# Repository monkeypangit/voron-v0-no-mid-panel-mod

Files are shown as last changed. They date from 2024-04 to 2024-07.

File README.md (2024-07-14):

# Voron Zero - No mid panel mod

&nbsp;<br>
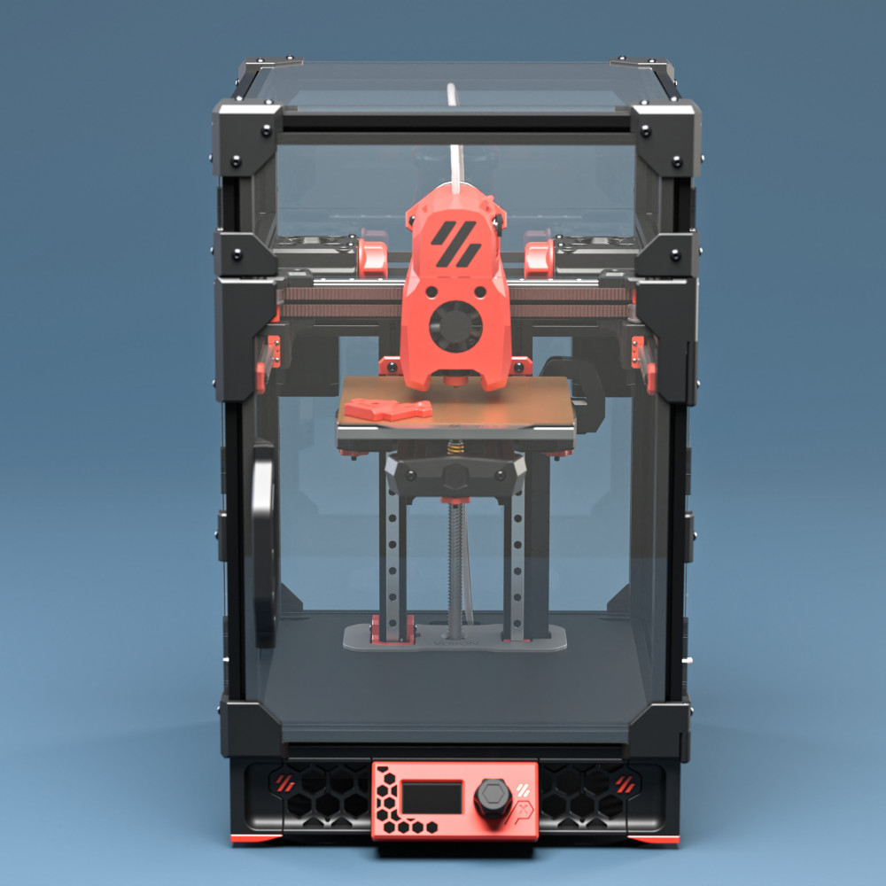
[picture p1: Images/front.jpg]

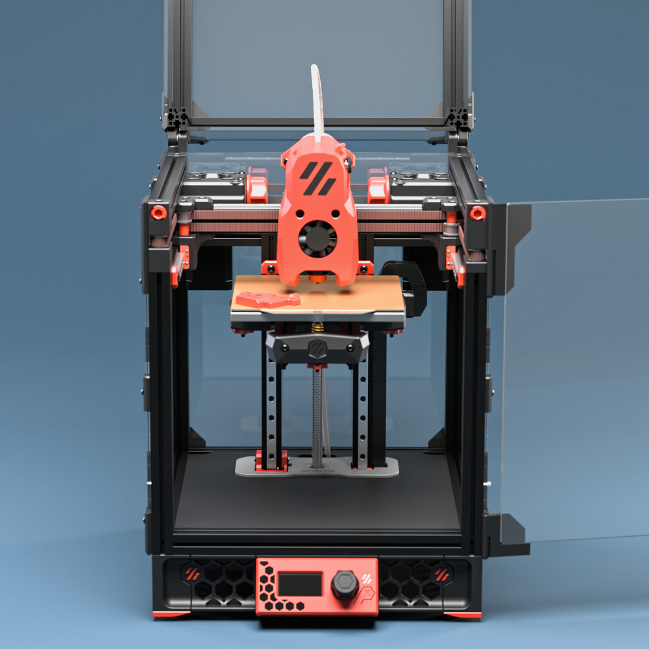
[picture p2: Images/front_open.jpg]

&nbsp;<br>
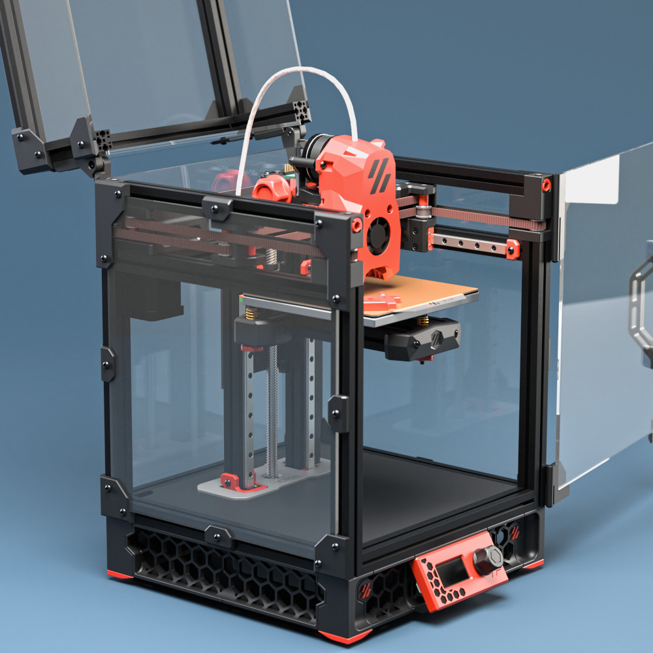
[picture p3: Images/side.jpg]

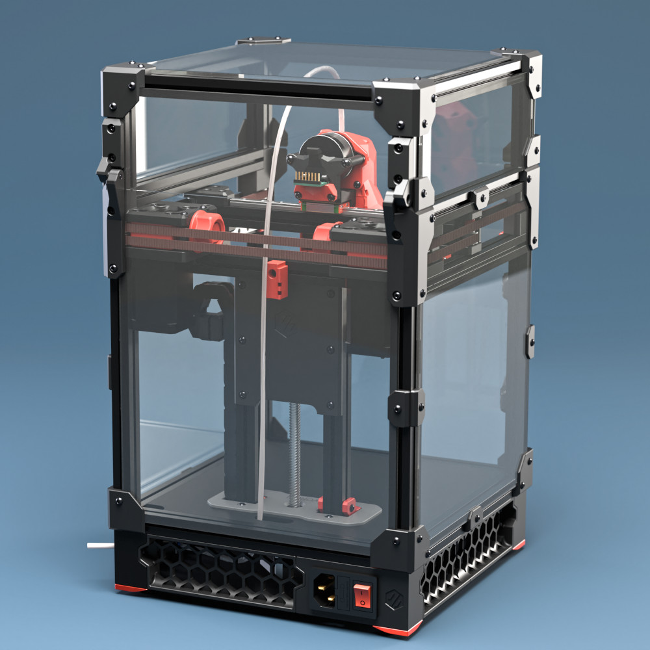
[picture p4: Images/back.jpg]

&nbsp;<br>

## Description
Mod for the Voron Zero that does away with the mid panel and replaces it with a printed brace.

## Status
This mod is in alpha/beta. It has only been built by me so far. There are some known issues listed below that may or may not be fixed at some point...

## Print settings
Print according to official Voron [print settings](https://docs.vorondesign.com/sourcing.html#print-settings).

## Bom
* Transparent back panel.
* Meanwell IRM-90-24ST power supply
* Crydom ED24C3 solid state relay
* Bigtreetech Manta E3EZ (SKR Pico + RPi stacked vertically also works)
* AC Powered bed heater
* 2x M3x35 BHCS
* 9x M3x8 BHCS
* 2x M3x6 BHCS
* 9x M3 Nut
* 8x M3 Brass heatstake inserts - short M3x5x4

## Z frame bracket
The trick to this mod is a printed bracket that connects the z extrusions to the back extrusion. It uses two M3x35 screws for rigidity instead of the lower blind joint screw pair in the stock version.
 
&nbsp;<br>
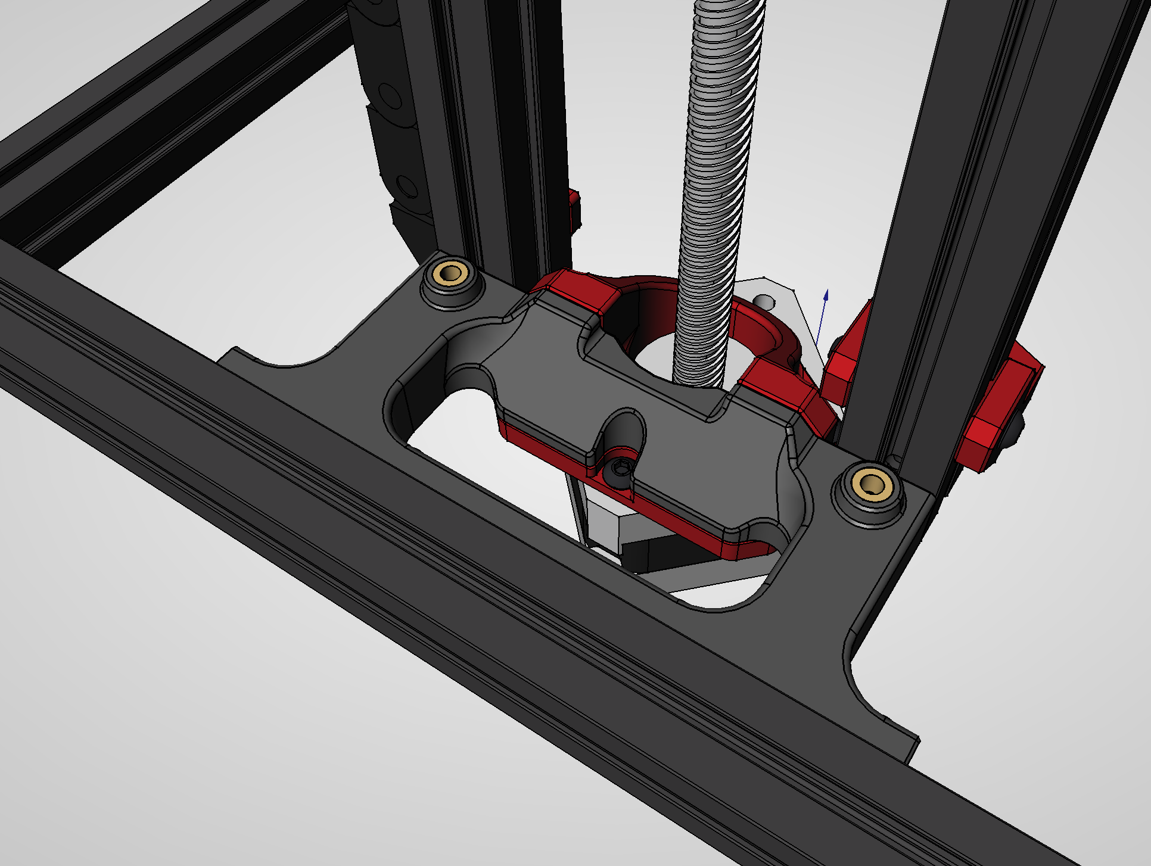
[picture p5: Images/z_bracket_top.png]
z bracket top

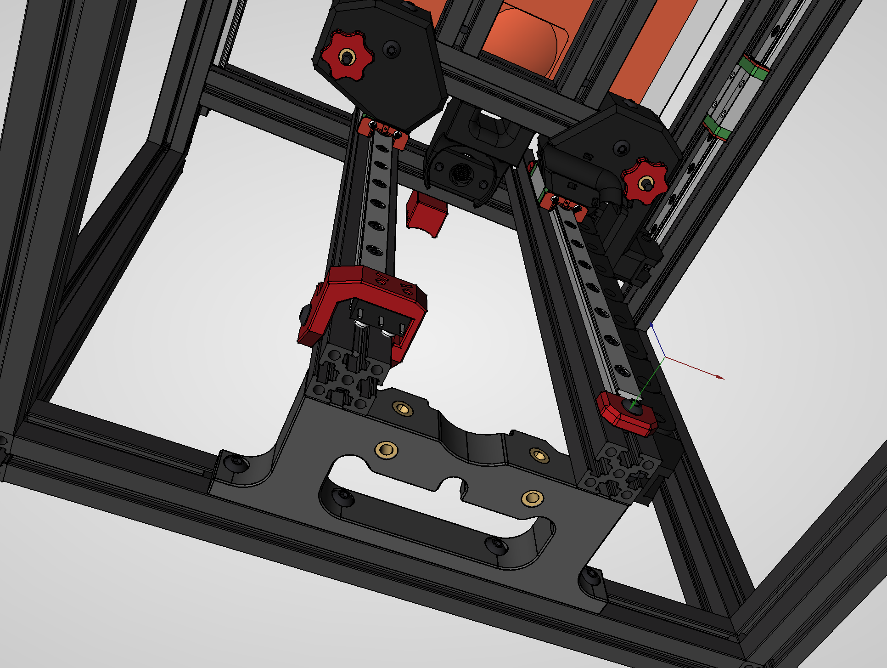
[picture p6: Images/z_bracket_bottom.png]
z bracket bottom

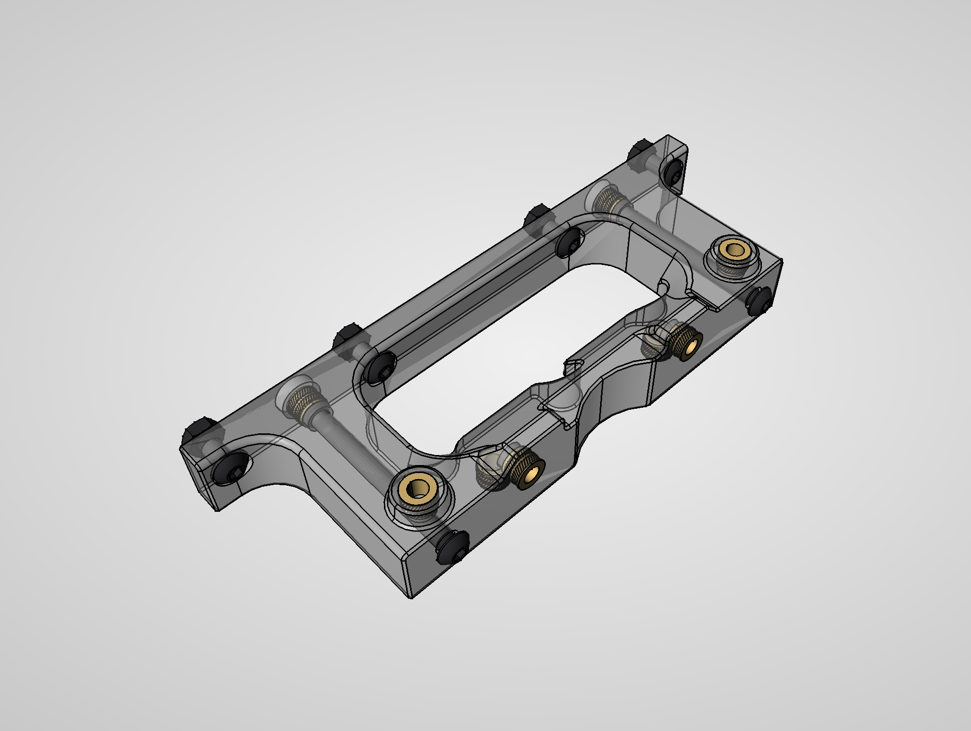
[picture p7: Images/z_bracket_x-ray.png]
z bracket x-ray

&nbsp;<br/>

## Build information
It is a fairly involved mod that requires replacing the power supply and heater from the stock BOM. It's probably best suited if you are building a self sourced v0 from scratch.

You need a working printer with a build surface that is large enough to print the 200x200mm deck panel.

The mod is designed to be as compatible as possible with other v0 mods. It retains as much as possible of the original parts.

All the electronics are moved to the bottom bay. This requires using a compact control board setup, a Meanwell IRM-90 power supply and an AC bed heater with a compact Crydom SSR.

This mod is somewhat finicky to assemble. You need to thread the deck panel and the cover plate over the z extrusions before you put the z brace in place. Here are some images go give you an idea of how the parts come together.

&nbsp;<br>
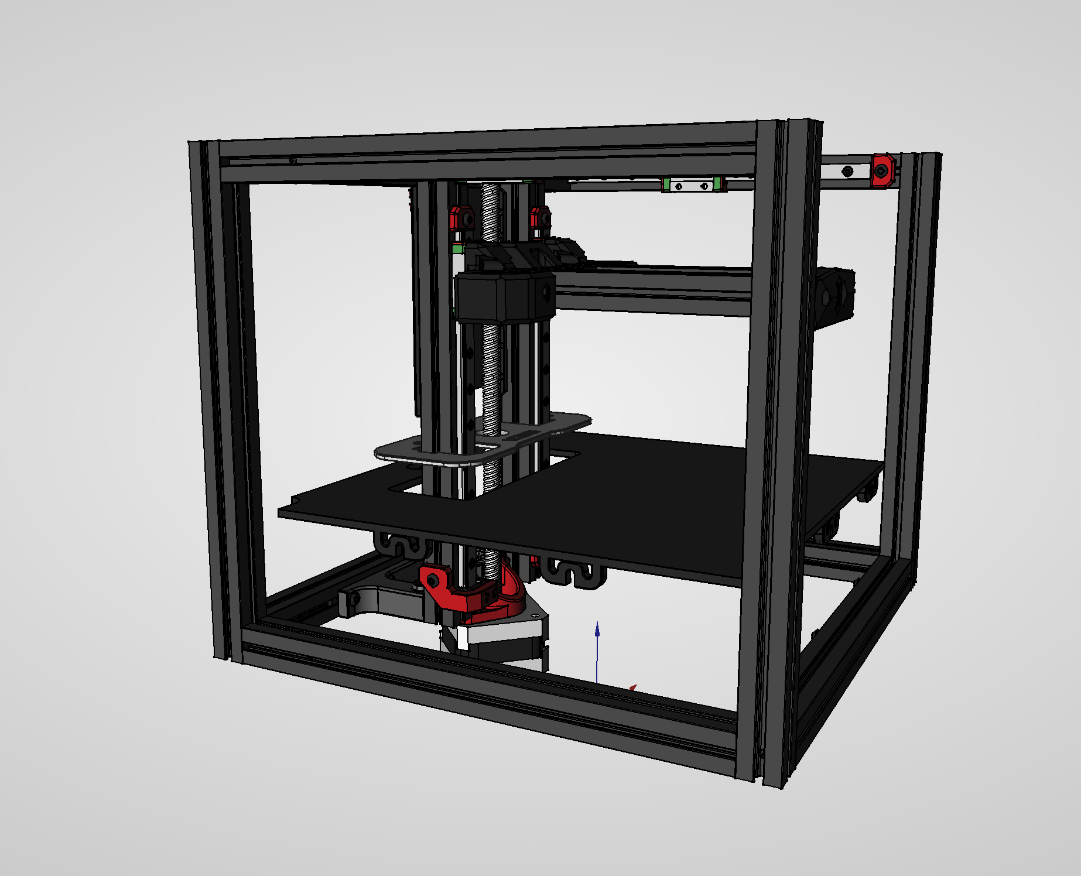
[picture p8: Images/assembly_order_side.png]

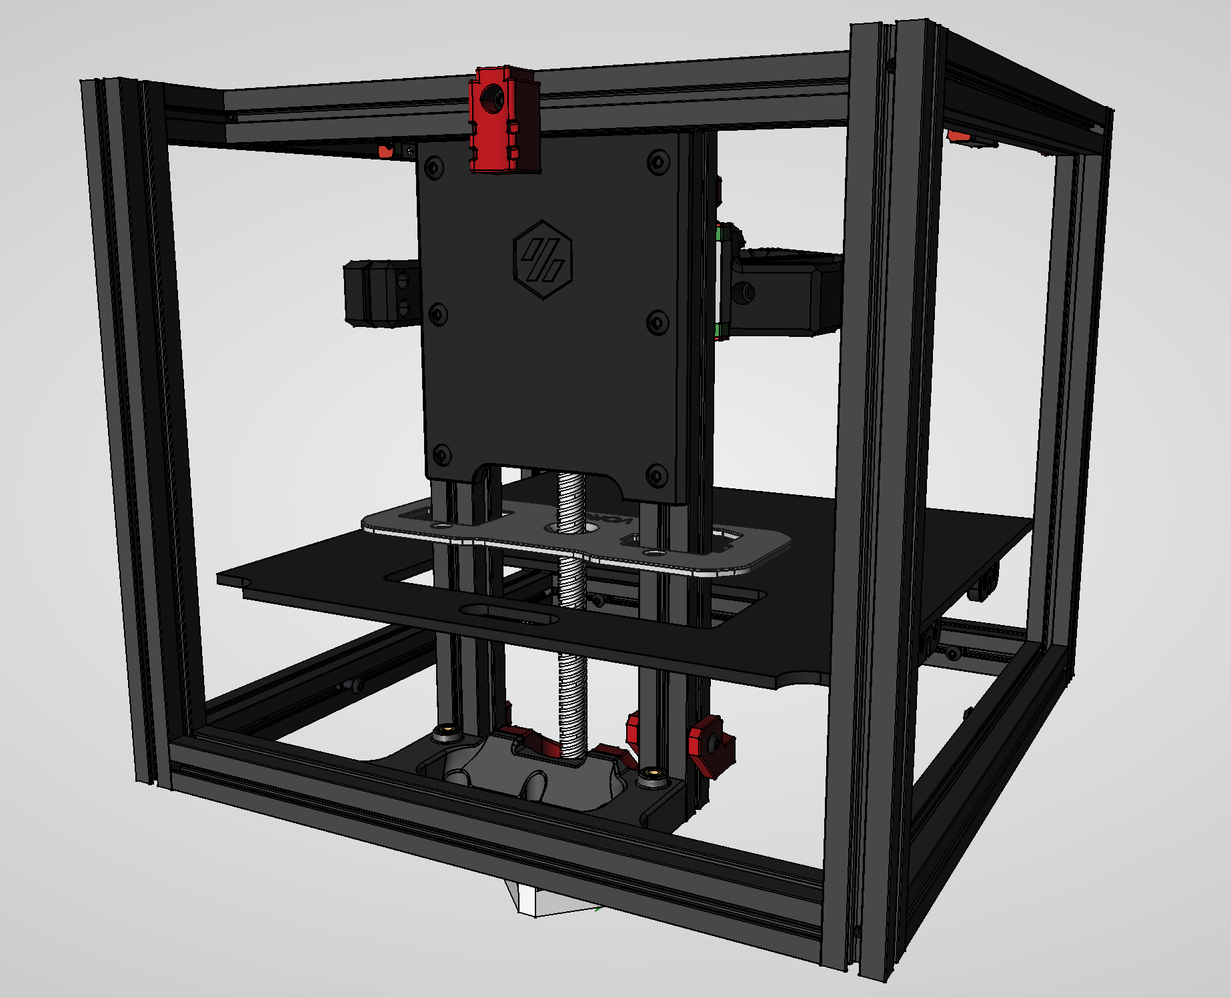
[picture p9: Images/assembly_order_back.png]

&nbsp;<br>

The printed deck panel has tabs for mounting to the bottom frame. The tabs allow for some flex to make sure the panel is rigidly mounted even if it is not exactly to size. It also has holes that allows the wires from the AB motors and toolhead to be passed through from the chamber to the electronics bay (see image below).

In the original V0 design the deck panel sits in the slot in the bottom frame. In this design the deck panel sits flush with the top of the extrusions in the bottom frame instead. You may loose a few millimiters of z-travel unless you are using a kirigami bed with a 6mm build plate and shorter bed screws.

I use this mod for a v0 build with a 170x120mm build plate (see image below). The 50mm wider frame size makes it easier to fit the compnents into the electronics bay. As far as I can tell the setup with an E3EZ should fit the stock size as well, but this is untested for now, so please do you own measurments before attempting this mod. The parts marked 170 in the stl folder is for a 170mm x build.

I recommend using a 2nd accent color for the deck panel cover if black is used as primary color.

This mod replaces the lower and upper back panel with a single transparent panel. There is no need to split these any more as there is no electronics bay in the back that requires access.

It is recommended to combine this mod with some type of fan skirt mod or to add a fan in the electronics bay (see issues).

## Chamber wiring
This image shows the intended routing of cables from the AB motors and toolhead to the electronics bay. There are cutouts in the deck panel to allow wires/cables to be passed through.

&nbsp;<br>
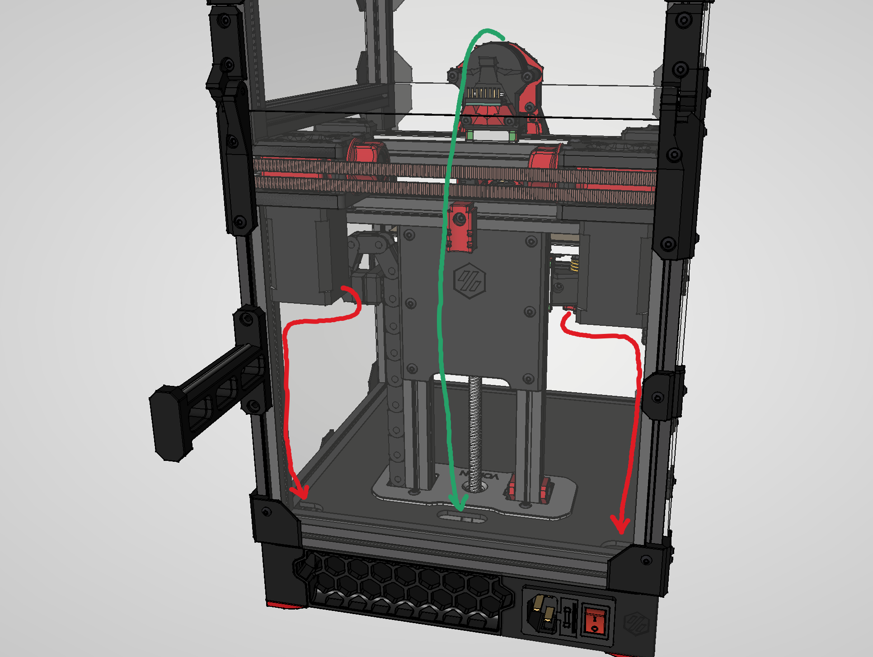
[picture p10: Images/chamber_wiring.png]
chamber wiring

&nbsp;<br/>

## Electronics bay
There are several controller boards/Pi configurations that will fit this mod. Just make sure to do some planning and measure twice oin the CAD model before you order parts.

You will have to find mounting brackets for your choice of components by yourself. I used a E3EZ with a CM4 in my build. There are STLs for the brackets for the IRM-90 and the E3EZ in the STLs folder. I stuck everything down to the deck panel with VHB tape.

Here is a youtube video by Steve Peterson where he builds a stock voron v0 with similar components for reference:

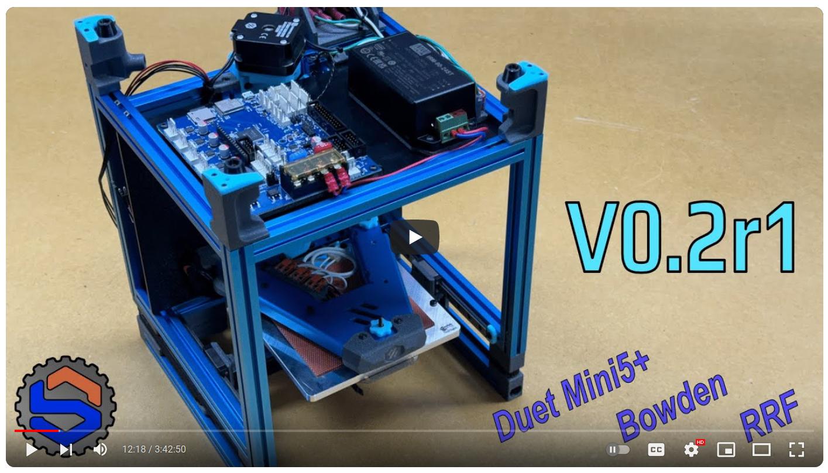
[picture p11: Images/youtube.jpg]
Steve Peterson builds a v0 with similar components


Note that he uses Reprap firmware with this build and thus he does not need a Raspberry Pi.

&nbsp;<br>
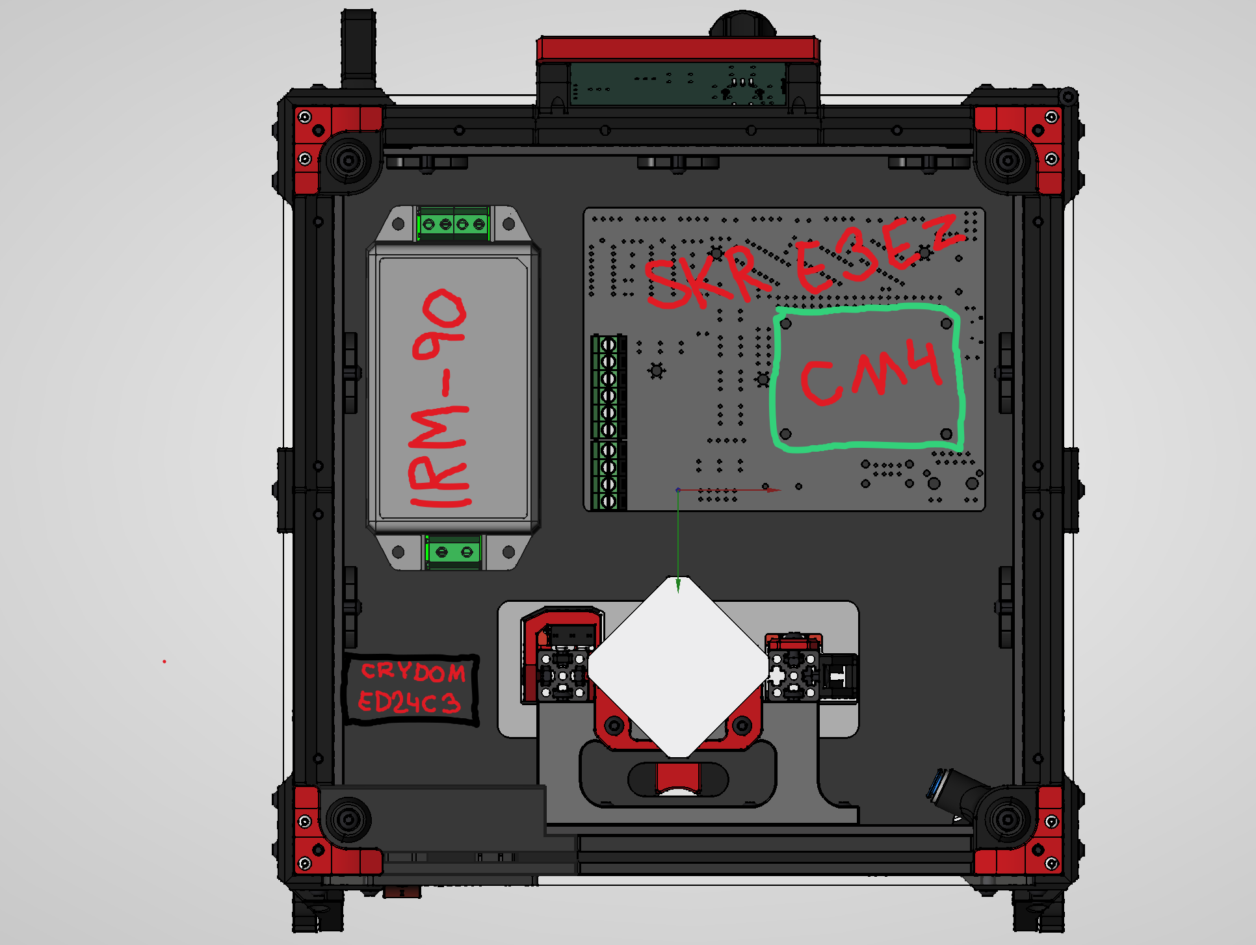
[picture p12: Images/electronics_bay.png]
electronics bay

&nbsp;<br/>

## Picture of build
Here is a picture of my build. It has a 170x120mm build area. That helps in fitting everything into the electronics bay, but from what I can measure it should work with a standard v0 as well.

I combined this with my quad cam lock mod that uses custom zero panels.

&nbsp;<br>
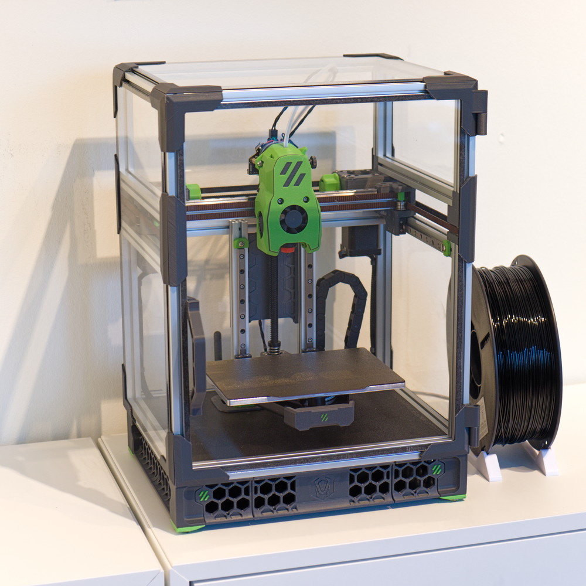
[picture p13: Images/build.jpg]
a picture of a Voron v0 with the mod installed

&nbsp;<br/>

## Known issues
* The inner pair of screws that hold the z frame bracket to the rear extrusion are tricky to reach. There are access holes for the allen key but it can be finicky...
* A split deck panel and cover would be good to simplify assembly/disassembly
* The electronics bay gets hot during pringing. I run AB motors at 0.5A RMS and Z motor at 0.3A RMS to keep things cool and sensorless homing from acting up. Probably need to add a fan somewhere in the electronics bay. There are fan skirt mods for the V0 that should fit this mod as well.
* Having the AB motors inside the enclosure makes sensorless homing more finicky to set up as the threshold values tend to vary with motor temperature.

## Disclamer
If you build this you do so at your own risk. I am not responsible if the design is incorrect or if something goes wrong. Please do your own research and act responsibly.

## Contact
Feel free to contact me here on github or as monkeyPan on the Voron Discord channel if you have questions or if you find any issues.

## Credit
Credit goes to the Voron Team for the original Voron Zero design.<br/>
[Voron team](https://github.com/VoronDesign/)<br/>

This project was inspired by the Itsy Bitsy printer by tigran on the Doomcube Discord channel.<br/>
[Itsy Bitsy by tigran](https://github.com/TigranDesigner/Voron-Mods/tree/main/Itsy%20Bitsy)

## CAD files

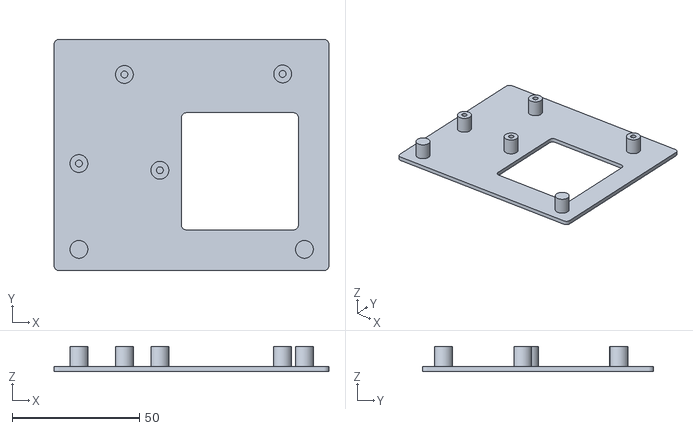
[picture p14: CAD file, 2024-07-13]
STLs/Electronics/Manta_E3EZ_Mount_x1.stl
108.0 x 90.8 x 10.0

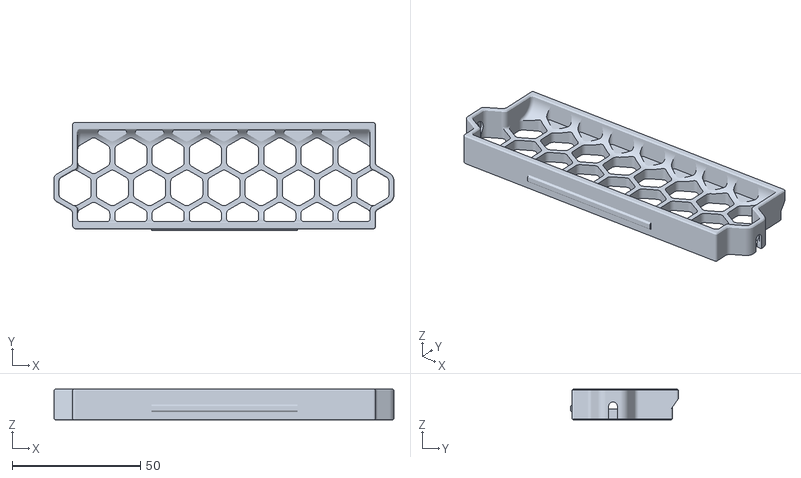
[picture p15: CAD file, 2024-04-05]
STLs/Skirts/Rear_Skirt_120_x1.stl
132.8 x 42.1 x 12.0

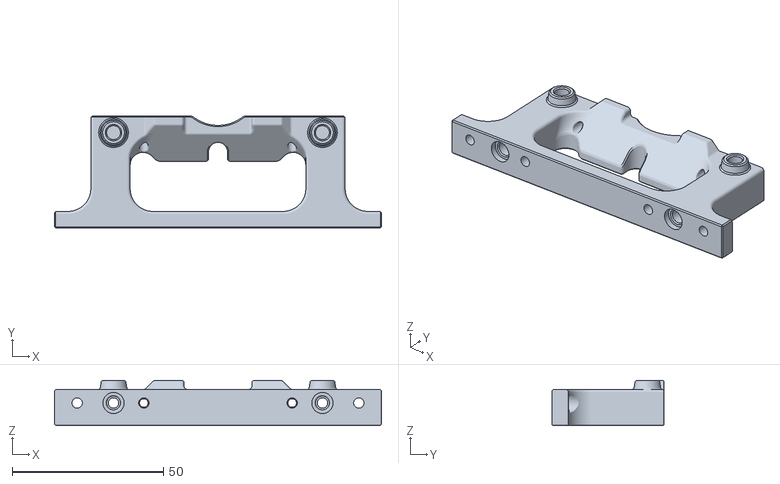
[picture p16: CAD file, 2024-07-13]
STLs/Z_Frame_Bracket_x1.stl
108.0 x 37.0 x 15.0

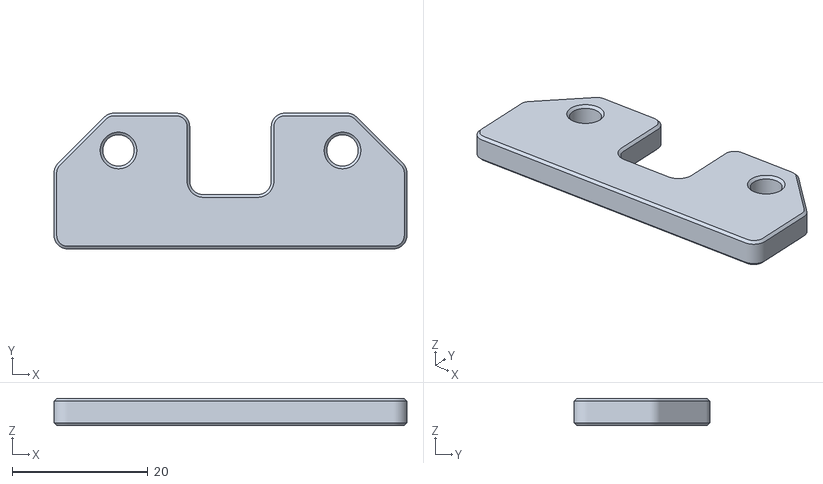
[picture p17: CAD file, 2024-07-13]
STLs/Electronics/IRM_90_24ST_Mount_x2.stl
52.0 x 20.0 x 4.00

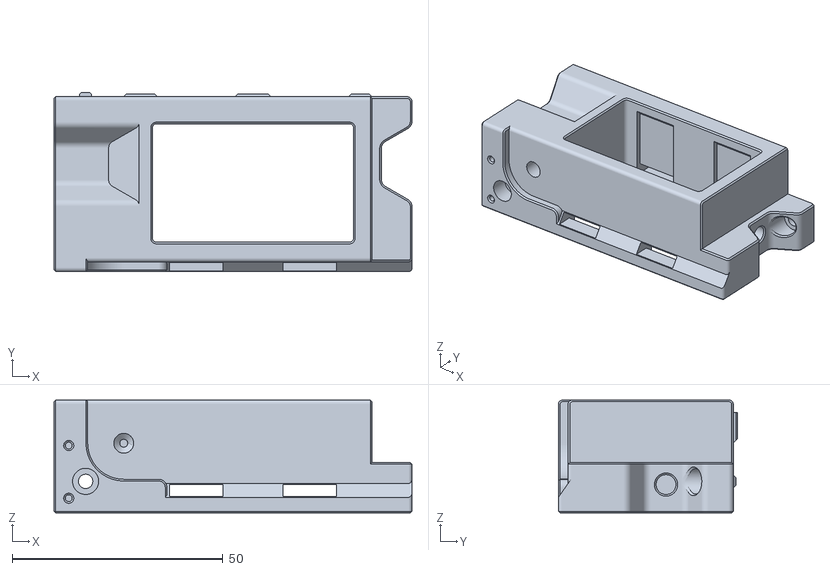
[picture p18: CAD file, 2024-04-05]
STLs/Skirts/Foot_Rear_Left_Inlet_x1.stl
84.9 x 42.5 x 26.8

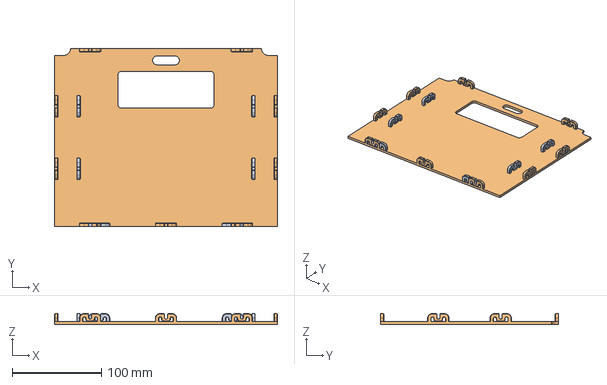
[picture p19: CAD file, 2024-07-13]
CAD/Deck Panel.FCStd
250.0 x 200.0 x 12.0 mm
Deck panel 120
Deck panel 170

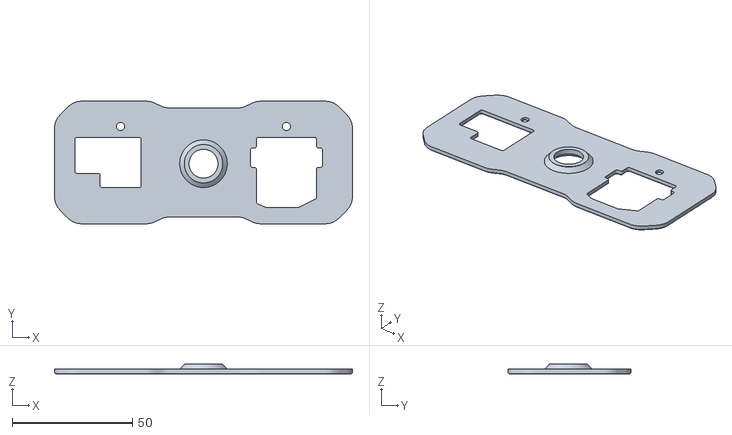
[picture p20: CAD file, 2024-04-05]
STLs/[a]_Deck Panel Cover_x1.stl
124.0 x 51.0 x 4.00

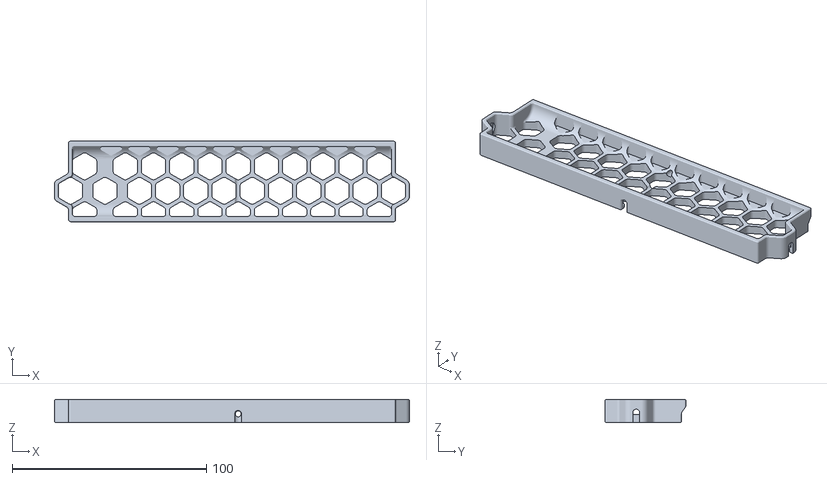
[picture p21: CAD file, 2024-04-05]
STLs/Skirts/Rear_Skirt_170_x1.stl
182.8 x 41.5 x 12.0

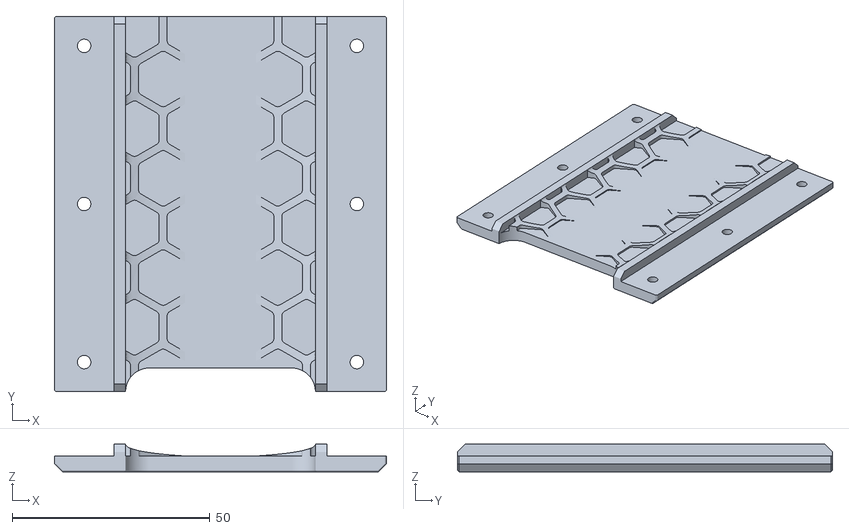
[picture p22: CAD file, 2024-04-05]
STLs/Mid_Panel_Brace_x1.stl
84.0 x 95.0 x 7.00

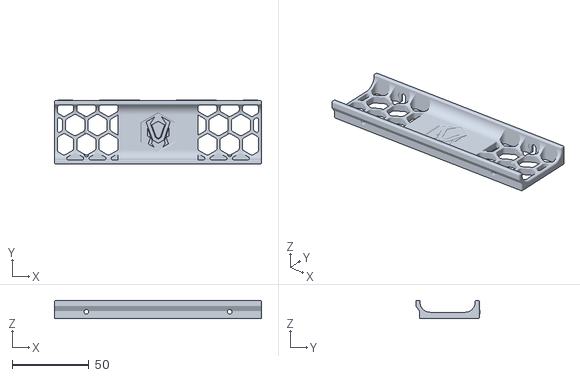
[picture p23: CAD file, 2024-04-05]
STLs/Skirts/Headless_Skirt_Insert_170_x1.stl
135.2 x 42.0 x 12.0

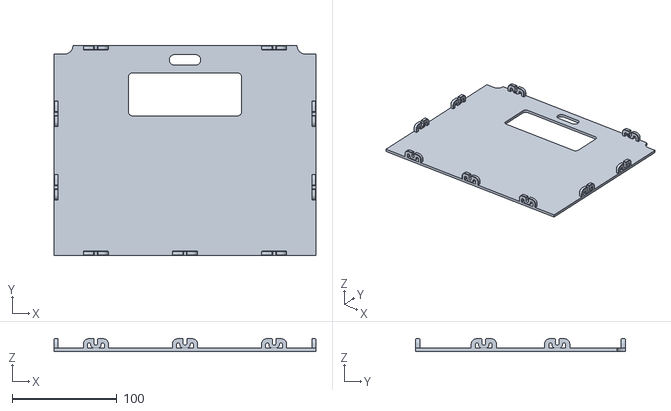
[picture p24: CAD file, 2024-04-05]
STLs/Deck_Panel_170_x1.stl
250.0 x 200.0 x 12.0

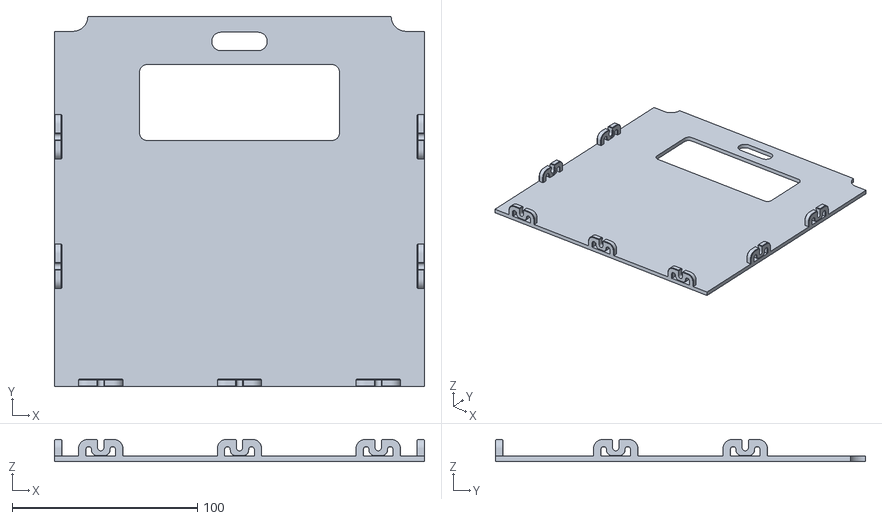
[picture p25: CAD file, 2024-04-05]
STLs/Deck_Panel_120_x1.stl
200.0 x 200.0 x 12.0

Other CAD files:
CAD/Mains Inlet Foot.FCStd
CAD/Z Frame Bracket.FCStd
CAD/Manta E3EZ Mount.FCStd
CAD/IRM-90-24ST Mount.FCStd
CAD/Deck Panel Cover.FCStd
CAD/Headless Front Skirt 170.FCStd
CAD/M2 Hex Adapter 170.FCStd
CAD/Mid Panel Brace.FCStd
CAD/Rear Skirt.FCStd
CAD/Z Frame Bracket Nut Adapter.FCStd
STLs/M2_Nut_Adapter_170_Rotated_x1.stl
STLs/Z_Frame_Bracket_Nut_Adapter_x1.stl
